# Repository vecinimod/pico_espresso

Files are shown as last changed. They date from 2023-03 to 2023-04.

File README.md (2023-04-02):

# pico espresso - $25 wifi enabled universal espresso machine PID +++ mod
A simple Raspberry Pi Pico W based espresso machine controller with support for:
+ Web interface with no addtional server (runs on mcu) using websockets for real time data
+ Shot graph generation in web ui and automatic shot timer
+ PID temperature control of boiler with duty cycled SSR
+ digital pump control profiles using PSM and robotdyn dimmer 
+ integrated shot scale with auto tareing and data recording in web app 
+ OLED display for current temperature, setpoint and SSR duty cycle
+ 1kg load cell compatible [scale case design and dimmer case](./scale/)
+ [flow meter](https://kh-technic.dk/wp-content/uploads/2020/02/AB32.pdf) measurement, logging and visualization
+ pressure transducer for real time pressure data

Can be installed on any espresso machine for temperature control but currently installed on a Calphalon temp iq

USE AT YOUR OWN RISK



picoesp





BOM ($25 to $100 depending on basic (ssr + pico + max6675) to complete (Add m6 tap, oled, load cell, dimmer, and transducer)
+ [OLED](https://www.amazon.com/gp/product/B072Q2X2LL/ref=ppx_yo_dt_b_asin_title_o00_s01?ie=UTF8&psc=1) $7
+ [SSR](https://www.amazon.com/gp/product/B08GPB7N2T/ref=ppx_yo_dt_b_asin_title_o01_s00?ie=UTF8&psc=1) $11
+ [pico w](https://www.microcenter.com/product/650108/raspberry-pi-pico-w) $6
+ [max6675](https://www.amazon.com/gp/product/B01HT871SO/ref=ppx_yo_dt_b_asin_title_o01_s00?ie=UTF8&psc=1) $7.69
+ [m6x1.0 tap and bit for thermocouple mounting on thermoblock using stock M4 hole location](https://www.amazon.com/uxcell-Spiral-Titanium-Machine-Threading/dp/B09TYS683J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) $9
+ [hx711 and 1kg load cell](https://www.amazon.com/gp/product/B08KRV8VYP/ref=ppx_yo_dt_b_asin_title_o07_s03?ie=UTF8&psc=1) $8
+ [robodyne zc triac dimmer](https://www.amazon.com/gp/product/B071X19VL1/ref=ppx_yo_dt_b_asin_title_o03_s00?ie=UTF8&psc=1) $15
+ [200 psi pressure transducer 1/8 npt](https://www.amazon.com/s?k=200+psi+pressure+transducer) $15
+ [1/8 npt female tee](https://www.amazon.com/Winmien-Fitting-Female-Diameter-Forged) $6
+ [1/8 npt to 4mm ptc connectors](https://www.amazon.com/IVLPHA-Connect-Pneumatic-Straight-Connectors/dp/B0B92BM32D) $10
+ [1k ohm and 2.2k ohm resistors](https://www.amazon.com/MCIGICM-Values-Resistor-Assortment-Resistors/dp/B06WRQS97C) $0.02 ($6 for assorment of 600)

Other parts and tools most people attempting this should already have on hand or have similar:
+ jst connectors and crimper
+ spade connectors and crimper
+ xt connectors (for wiring harness connecting mains to ssr, thermoblock)
+ 24 gauge high temp silicone coated wire
+ wire stripper
+ multimeter (handy for chasing down faulty wires and connections)
+ oscilloscope (e.g. to check flowmeter and dimmer function)
+ soldering iron
+ heat shrink tubing
+ electrical tape
+ 3d printer (for scale and cases for pico and dimmer)
+ thermal paste for thermocouple
+ donor usb cables
+ 5W usb power supply
+ [pico w shield/breadboard](https://www.amazon.com/Treedix-Compatible-Raspberry-Breakout-Flexible/dp/B091F7YSCD)

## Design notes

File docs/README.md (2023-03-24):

# Installation of software on pico w
1. Install Micropython on your pico w
2. Install the following using thonny's package manager:
    1. [picozero](https://github.com/RaspberryPiFoundation/picozero)
    2. [ssd1306](https://github.com/stlehmann/micropython-ssd1306/blob/master/ssd1306.py)
    3. [uasyncio](https://github.com/peterhinch/micropython-async/blob/master/v3/docs/TUTORIAL.md)
3. Install [microdot](https://github.com/miguelgrinberg/microdot), and it's websocket, async, and async websocket helper libraries by copying the files from github in the src folder of project that correspond to these (4 files total for microdot)
4. Add contents of lib from this project to the pico's lib directory (max6675.py, PID.py, hx711_pio.py and secrets.py)
5. Edit secrets.py accordingly for your network
6. copy main.py to your pico w
7. determine your scale factor for the loadcell and edit line 28 of main.py

# Pinout guides for each peripheral

| Max6675 | GND | VCC  | SCK | CS | SO |
| --- | --- | ---- | --- | --- | --- |
| MCU PIN Name | GND | 3.3v | GPIO21 | GPIO20 | GPIO19 |
| MCU PIN # | 23  | 36 | 27 | 25 | 24 |

| SSR | +  | \- |
| --- | -- | -- |
| MCU PIN Name | GPIO2  | GND |
| MCU PIN # | 4 | 3 |

| AB32 Flowmeter  | output | ground | 5V In |
| --- | --- | --- | ----- |
| Logic converter | HV2 | | |
| MCU PIN Name | | GND | VSYS  |
| MCU PIN # | | 38 | 39 |

| Logic converter | HV | ground | LV | LV2 |
| --- | ---- | --- | ---- | ----- |
| MCU PIN Name | VSYS | GND | 3.3v | GPIO3 |
| MCU PIN # | 39 | 38 | 36 | 5 |

| HX711 | GND | DT | SCK | VCC  |
| --- | --- | ----- | ----- | ---- |
| MCU PIN Name | GND | GPIO6 | GPIO5 | 3.3v |
| MCU PIN # | 8 | 9 | 7 | 36 |

| Robotdyn Dimmer | VCC  | GND | ZC | PSM | OUT | N | IN |
| --- | ---- | --- | --- | --- | --- | --- | ---- |
| Mains | | | | | | neutral | live |
| Pump | | | | | large gauge wire | pump thin gauge | |
| MCU PIN Name | 3.3v | GND | GPIO13 | GPIO12 | | | |
| MCU PIN # | 36 | 18  | 17 | 16 | | |

| OLED | GND | VCC  | SCL | SDA |
| --- | --- | ---- | --- | --- |
| MCU PIN Name | GND | 3.3v | GPIO15 | GPIO14 |
| MCU PIN # | 18  | 36 | 20 | 19 |

| Steam Button | Wire 1 | Wire 2 |
| --- | --- | --- |
| MCU PIN Name | GPIO9  | GND |
| MCU PIN # | 12 | 13 |

| Shot button  | Wire 1 | Wire 2 |
| --- | --- | --- |
| MCU PIN Name | GPIO10 | GND |
| MCU PIN # | 14 | 13 |

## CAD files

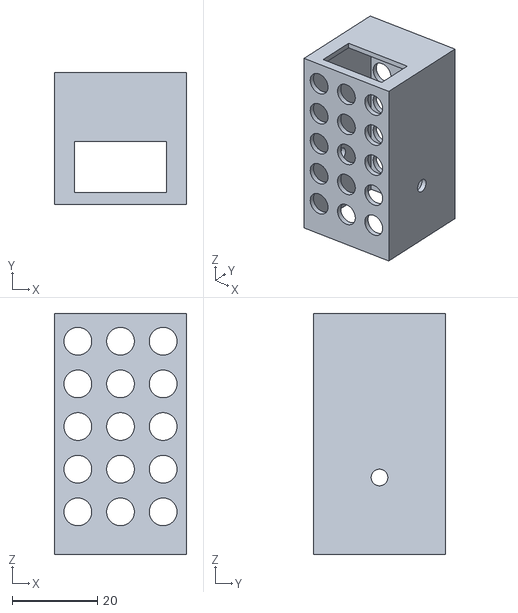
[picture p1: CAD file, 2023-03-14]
scale/dimmercase.stl
31.0 x 31.0 x 56.5

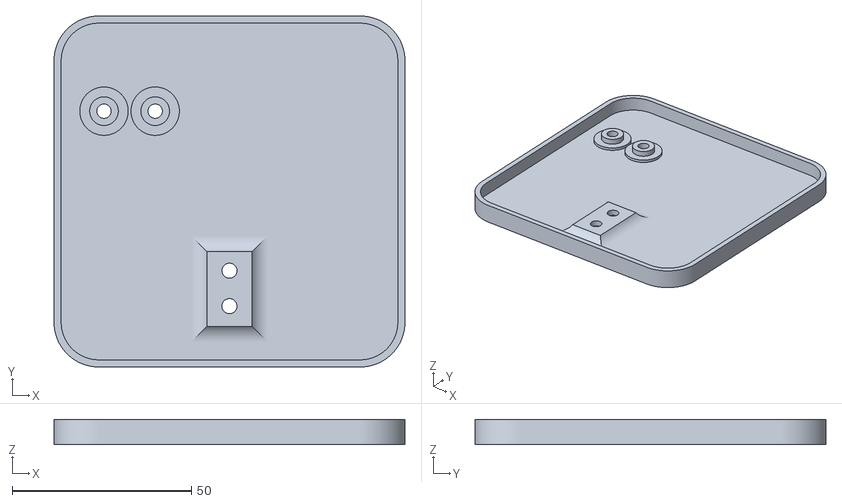
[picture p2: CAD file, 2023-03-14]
scale/bottom plate.stl
98.0 x 98.0 x 7.00

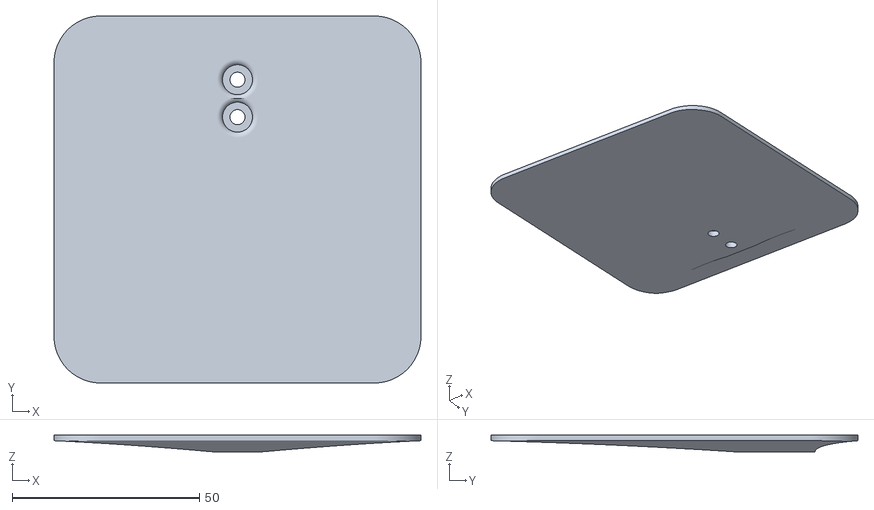
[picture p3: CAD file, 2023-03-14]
scale/topplate.stl
98.0 x 98.0 x 4.50

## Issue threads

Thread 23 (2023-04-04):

make hw config class

vecinimod, 2023-04-04:
the current setup uses default values for all pins - this could break the board or potentially peripherals for new setups
let's create an object so that we can do, e.g. the following in the pico_espresso init
```
class pinout:
    __init__(self):
        self.heater_pin = 2 #<- user configured class attributes here or read from yaml or json
        ...
class pico_espresso:
    __init__(self, pinout_instance):
    self.pinout = machine_pinout
    self.my_heater = heater(...,mypin=self.pinout.heater_pin)
    ...
```
then a new pico is
```
my_pico = pico_espresso(machine_pinout = pinout(),...)
```

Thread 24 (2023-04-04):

make watchdog for thermocouple not sensing temperature rise

vecinimod, 2023-04-04:
Protect for the condition where thermal runaway due to fault in sensing heat - may need a debug flag that turns this off when running without mains plugged in

vecinimod, 2023-04-04:
some examples of how to implement for drops in temperature and increases in temperature, but for an espresso machine this is more complicated due to stages
https://jgaurorawiki.com/thermal-runaway

vecinimod, 2023-04-04:
probably implement in steam one way (turn off steam for sure at certain timeout- add stage in profile create first line of defense) and then shots another way - preheat will also be a problem

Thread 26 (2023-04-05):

modify stage logic to have preheat be a normal stage

vecinimod, 2023-04-05:
workflow is broken for second shot after steam, as machine is still very hot, need to have preheat pump water to cool/stabilize temperature for both steam and shot

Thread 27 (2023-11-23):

max6675.py

ovimoc, 2023-11-23:
Hi,
My name is Ovidiu (ovimoc@yahoo.com),
I'm trying to take small steps with your project.
"max6675.py" seems to be missing in the "lib" directory
In the first phase, I would like to be able to monitor the temperature, weight and pressure and view the graphs on the web page.
I followed the installation steps described by you, for "uasyncio" I did not succeed with thonny's package manager but with:
"import mip
mip.install("github:peterhinch/micropython-async/v3/primitives")
mip.install("github:peterhinch/micropython-async/v3/threadsafe")"
I would like to know if it is ok?
Thank you,
I wish you a good day.

dvalentino20, 2023-11-25:
Hi for some reason I can't push a file to the repo, but here's the code for max6675.py. I am not sure about how you installed usasnycio, the only way to know if it works is to try it
```
import time
class MAX6675:
    MEASUREMENT_PERIOD_MS = 220

    def __init__(self, sck, cs, so):
        """
        Creates new object for controlling MAX6675
        :param sck: SCK (clock) pin, must be configured as Pin.OUT
        :param cs: CS (select) pin, must be configured as Pin.OUT
        :param so: SO (data) pin, must be configured as Pin.IN
        """
        # Thermocouple
        self._sck = sck
        self._sck.low()

        self._cs = cs
        self._cs.high()

        self._so = so
        self._so.low()

        self._last_measurement_start = 0
        self._last_read_temp = 0
        self._error = 0

    def _cycle_sck(self):
        self._sck.high()
        time.sleep_us(1)
        self._sck.low()
        time.sleep_us(1)

    def refresh(self):
        """
        Start a new measurement.
        """
        self._cs.low()
        time.sleep_us(10)
        self._cs.high()
        self._last_measurement_start = time.ticks_ms()

    def ready(self):
        """
        Signals if measurement is finished.
        :return: True if measurement is ready for reading.
        """
        return time.ticks_ms() - self._last_measurement_start > MAX6675.MEASUREMENT_PERIOD_MS

    def error(self):
        """
        Returns error bit of last reading. If this bit is set (=1), there's problem with the
        thermocouple - it can be damaged or loosely connected
        :return: Error bit value
        """
        return self._error

    def read(self):
        """
        Reads last measurement and starts a new one. If new measurement is not ready yet, returns last value.
        Note: The last measurement can be quite old (e.g. since last call to `read`).
        To refresh measurement, call `refresh` and wait for `ready` to become True before reading.
        :return: Measured temperature
        """
        # Check if new reading is available
        if self.ready():
            # Bring CS pin low to start protocol for reading result of
            # the conversion process. Forcing the pin down outputs
            # first (dummy) sign bit 15.
            self._cs.low()
            time.sleep_us(10)

            # Read temperature bits 14-3 from MAX6675.
            value = 0
            for i in range(12):
                # SCK should resemble clock signal and new SO value
                # is presented at falling edge
                self._cycle_sck()
                value += self._so.value() << (11 - i)

            # Read the TC Input pin to check if the input is open
            self._cycle_sck()
            self._error = self._so.value()

            # Read the last two bits to complete protocol
            for i in range(2):
                self._cycle_sck()

            # Finish protocol and start new measurement
            self._cs.high()
            self._last_measurement_start = time.ticks_ms()

            self._last_read_temp = value * 0.25

        return self._last_read_temp
```

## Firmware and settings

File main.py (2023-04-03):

import time
from json import dumps as jdump
from machine import Pin, Timer, I2C, ADC
from ssd1306 import SSD1306_I2C
from max6675 import MAX6675
from picozero import Button
from PID import PID #https://github.com/gastmaier/micropython-simple-pid/blob/master/simple_pid/PID.py
from microdot_asyncio import Microdot, Response, send_file
from microdot_asyncio_websocket import with_websocket
import uasyncio as asyncio
from random import randint
import network
from secrets import secrets
from hx711_pio import HX711

#https://stackoverflow.com/questions/74758745/how-to-run-python-microdot-web-api-module-app-run-that-is-already-an-asyncio


pin_OUT = Pin(6, Pin.IN, pull=Pin.PULL_UP)
pin_SCK = Pin(5, Pin.OUT)

hx711 = HX711(pin_SCK, pin_OUT)
#scale = 300
hx711.tare(3)
hx711.set_time_constant(.95)

def callhx2():
    value = hx711.get_value()/741.263
    return(value)
# print(callhx2())
# time.sleep_ms(3000)
# print(callhx2())

class pressure:
    def __init__(self, adcpin=1):
        self.adc=ADC(1)
    
    def read(self):
        self.volts = self.adc.read_u16() * 3.3 / 65535 #volts
        self.psi = (self.volts - .344)/(3.094-.344)*200
        self.bar = self.psi / 14.5038

    def get_bar(self):
        self.read()
        return(self.bar)

class flowmeter:
    def __init__(self, pinin=3):
        self.pin_IN = Pin(pinin, Pin.IN, pull=Pin.PULL_DOWN )
        self.last_time=0
        self.count= 0
        self.flow=0
        self.pin_IN.irq(trigger=self.pin_IN.IRQ_RISING, handler=self.update_flow)


    def update_flow(self,pin):
        self.count +=1
        
    def compute_flow(self):
        if(self.last_time==0):
            self.last_time=time.ticks_ms()
            self.last_count=self.count
            flow = 0
        else:
            this_time = time.ticks_ms()
            dt = time.ticks_diff(this_time, self.last_time)
            dct = self.count - self.last_count
            mlx1000 = .5195 * dct #1000ths of ml i.e. microliters
            flow = mlx1000 / (dt/1000)
            self.last_time = this_time
            self.last_count = self.count
        self.flow = flow

# pin_IN = Pin(3, Pin.IN, Pin.PULL_DOWN )
# def update_flow(pinn):
#     print("floooow")
# pin_IN.irq(trigger=pin_IN.IRQ_RISING, handler=update_flow)

# Replace the following with your WIFI Credentials
secrets = secrets()
SSID = secrets.SSID
SSI_PASSWORD = secrets.SSI_PASSWORD

def do_connect():
    import network
    sta_if = network.WLAN(network.STA_IF)
    if not sta_if.isconnected():
        print('connecting to network...')
        sta_if.active(True)
        sta_if.connect(SSID, SSI_PASSWORD)
        while not sta_if.isconnected():
            pass
    print('Connected! Network config:', sta_if.ifconfig())

so = Pin(19, Pin.IN)
sck = Pin(21, Pin.OUT)
cs = Pin(20, Pin.OUT)
 
max = MAX6675(sck, cs , so)
async def get_temp():
    data= max.read()
    return data
class oled_ctl:
    def __init(self, sda, scl, pwr):
        return
    def update(self, setpoint, input_, output):
        return
    
class oled_ctl_old:
    def __init__(self,sda, scl, pwr):
        i2c=I2C(1,sda=Pin(sda), scl=Pin(scl), freq=400000)
        self.oled = SSD1306_I2C(128, 64, i2c)
        self.pwr = Pin(pwr, Pin.OUT)
        self.pwr.high()
    def update(self, setpoint, input_, output):
        self.oled.fill(0)
            
        if(setpoint == 0):
            target = "SLEEPING"
        else:
            target = "Set Temp {target:.1f}"
            target = target.format(target = setpoint*1.8+32)                

        cur = "Mes Temp {cur:.1f}"
        if(input_ is None):
            cur = cur.format(cur = 0)
        else:
            cur = cur.format(cur = input_*1.8+32)
        
        duty = "Power Out {duty:.1f}%"                
        if(output is None):
            duty = duty.format(duty = 0)
        else:
            duty = duty.format(duty = output)                
            
        self.oled.text("VALENTINO Caffe", 0, 0)
        self.oled.text(target, 0, 16)
        self.oled.text(cur, 0, 32)
        self.oled.text(duty, 0, 48)
        self.oled.show()

class ssrCtrl:
    def __init__(self, WindowSize, mypid, mypin, oled):
        self.WindowSize = WindowSize
        self.pulsewidth = 20
        self.maxpulsespersec = WindowSize / self.pulsewidth #for sample period, how often can we
        self.high = False
        self.last_read = 0
        self.end_fire = 0
        self.mypid = mypid
        self.mypin = mypin
        self.oled=oled
        self.weight = 0
        

    def calc_pulse(self, temp):
        if(self.mypid.setpoint - temp > 5):
            self.output=100
        elif(temp - self.mypid.setpoint > 5):
            self.output = 0
        else:
            self.output = self.mypid(temp)
            
        print("input", temp, "setpoint", self.mypid.setpoint, "output", self.output)
        
        if(self.output is None):
            self.target_pulse = 0.1 #
        else:
            self.target_pulse = self.maxpulsespersec * self.output / 100 + 0.1 # number of pulses to fire on out of possible in sample period
        if(self.target_pulse > self.maxpulsespersec):
            self.target_pulse = self.maxpulsespersec
        self.fire_every_pulses = self.maxpulsespersec / self.target_pulse
        self.fire_every_ms = self.pulsewidth * self.fire_every_pulses
            
    async def pulse(self):
        now = time.ticks_ms()

        if(self.last_read==0 or now - self.last_read > self.WindowSize):        #new measurement and target pulse
            self.mypin.low()
            self.last_read = now
            temp=await get_temp()
            self.calc_pulse(temp)    
            self.oled.update(self.mypid.setpoint, await get_temp(), self.output)
            
        if(self.target_pulse >= 1 and self.output < 100): #calling for output

            if(now > self.end_fire ):
                #end pulse          
                self.mypin.low()
                self.high = False
            
            if self.end_fire==0 or (now > self.next_fire and not self.high):
                #new pulse now set it up
                self.start_fire = time.ticks_ms()
                self.end_fire = self.start_fire + self.pulsewidth
                self.next_fire = self.end_fire + self.fire_every_ms
                self.mypin.high()
                self.high = True
                
        elif(self.output==100):
            self.mypin.high()
    
    def reset(self):
        if(self.target_pulse>0):
            self.target_pulse = 0
            self.output = 0
            self.last_read = 0 

#define app
#https://www.donskytech.com/using-websocket-in-micropython-a-practical-example/
#https://stackoverflow.com/questions/74758745/how-to-run-python-microdot-web-api-module-app-run-that-is-already-an-asyncio
app = Microdot()
Response.default_content_type = 'text/html'

@app.route('/')
async def index(request):
    asyncio.sleep_ms(1)
    print("index request")
    return send_file('index.html')

@app.route('/echo')
@with_websocket
async def echo(request, ws):
    while True:
        asyncio.sleep_ms(1)
        data = await ws.receive()
        print(data)
        target = "Set Temp {target:.1f}"
        my_espresso.set_shot_temp(int(data))
        target = target.format(target = my_espresso.user_shot_temp)
        asyncio.sleep_ms(1)
        await ws.send(target)
        
@app.route('/mode')
@with_websocket
async def echo(request, ws):
    while True:
        asyncio.sleep_ms(100)
        data = await ws.receive()
        print(data)
        asyncio.sleep_ms(1)
        hx711.tare(3)
        if(my_espresso.mode == "shot"): #check machine mode has to be in shot mode
            my_espresso.ui_mode_change_request()
        else:
            print("Error gui asked for shot mode when not physically in shot mode, turn dial")
        
@app.route('/data')
@with_websocket
async def data(request, ws):    
    while True:
        await asyncio.sleep_ms(my_espresso.sample_period)
        temp = await get_temp()
 
        weight = callhx2()
        myflow.compute_flow()
        data_str = jdump({"time":my_espresso.mode_elapsed_time/1000,"temperature":temp,
                          "output":my_espresso.myssr.output, "setpoint":my_espresso.mypid.setpoint,
                          "weight":weight, "mode":my_espresso.mode,"mode_change":my_espresso.flag_ui_mode_change,
                          "pump_output":my_espresso.mypump.output,
                          "flow":myflow.flow, "pressure":mypressure.get_bar()})
        my_espresso.flag_ui_mode_change = False
        await ws.send(data_str)

        
class pump:
    def __init__(self, profile, psm):
        self.profile = profile
        self.stage = 0
        self.time_start_stage=0
        self.psm = psm
        self.output=0
        self.set_profile(profile)
    
    def set_profile(self, profile):
        self.profile = profile
        cumultime = 0

        for k in sorted(self.profile.keys()):
            self.profile[k]["start"] = cumultime 
            self.profile[k]["end"] = cumultime + self.profile[k]["duration"]
            cumultime = self.profile[k]["end"]

        print("updated pump profile:", self.profile)
    
    def update_shot_pump_output(self, time_ms, mass):
        _output = -1
        time_s = time_ms / 1000
        if(self.stage == 0):
            self.time_start_stage = time_s
            self.stage=1
            
        if(mass<0):
            mass = 0
            
        if(self.stage<=len(self.profile)):            
            if(time_s - self.time_start_stage > self.profile[self.stage]["duration"] or self.profile[self.stage]["max_mass"] < mass):
                self.stage += 1
                self.time_start_stage = time_s
            if(self.stage<=len(self.profile)):         
                self.output = ((time_s - self.time_start_stage) / self.profile[self.stage]["duration"]) * (self.profile[self.stage]["pump_end"] - self.profile[self.stage]["pump_start"]) + self.profile[self.stage]["pump_start"]
        else:
            self.output = 0

    def run_pump(self, start_time, current_time, mass_update_intvl=250):
        timenow = time.ticks_diff(current_time, start_time)
        if(timenow<100):
            self.mass=0
        if(timenow%mass_update_intvl<=10):
            self.mass = callhx2()
        self.update_shot_pump_output(timenow, self.mass)
        self.psm.set_output(self.output)
#         if(self.stage<=len(self.profile) and timenow%1000==0):
#         if(timenow%1000==0):
#             myflow.compute_flow()
#             if(self.stage<=len(self.profile)):
#                 print("time", timenow/1000,"stage",self.profile[self.stage]["name"],
#                       "output", self.output, "mass", self.mass, "flowct", myflow.count,
#                       "flow", myflow.flow)
#         else:
#             return
    def reset(self):
        self.psm.set_output(0)
        self.stage=0
        
    def test_output(self):
        startt=time.ticks_ms()
        timeno = 0
        mass=0
        
        while(True):
            timeno = time.ticks_diff(time.ticks_ms(),startt)
            self.update_shot_pump_output(timeno, mass)
            self.psm.set_output(self.output)
            if(timeno % 1000 == 0):
                mass = callhx2()
                if(self.stage<=len(self.profile)):
                    print("time", timeno/1000,"stage",self.profile[self.stage]["name"], "output", "shoto", self.output, "selfo", self.output, "mass", mass)
                else:
                    return

class psm:
    def __init__(self, psm_pin=12, zc_pin=13):
        self.psm_pin = Pin(psm_pin, Pin.OUT)
        self.zc_pin = Pin(13, Pin.IN, pull=Pin.PULL_DOWN)
        self.zc_pin.irq(trigger=self.zc_pin.IRQ_RISING, handler=self.pulse)
        self.high=False
        self.output=0
        self.start_time= time.ticks_ms()
        self.last_fire = self.start_time
        self.count=0
        self.mypid = PID(40, 0.05, 0.05, setpoint=10, scale='ms',
                         output_limits=[0, 100], proportional_on_measurement=False)

    def set_output(self, req_output):
        if(req_output > 100):
            req_output = 100
        elif(req_output < 0):
            req_output = 0
            
        self.output = req_output

    def pulse(self, pin):
        if(self.output==100):
            self.psm_pin.high()
        else:
            if(self.count*100 % (10000//(100-self.output)) < 100): # ct * 100 % (100//((100-output)*100))
                self.psm_pin.low()
            else:
                self.psm_pin.high()
                
        if(self.count==100):
            self.count=1
        else:
            self.count+=1
        
    def sim(self):
        oo = 0
        startt=time.ticks_ms()
        timeno = 0
        input=0
        while(True):
            timeno = time.ticks_diff(time.ticks_ms(),startt)
            input = timeno/100000 *.2 * oo - randint(0,100)/50
            if(input<0):
                input = 0
            if(input>10):
                input=10
            if(timeno % 1000 == 0):
                oo = self.mypid(input)
                print("time", timeno, "input",input, "output", oo, "seto", self.output)
                self.set_output(oo)
            
        
# a class to manage the loop, run both control + sensor and app tasks
class espresso:
    def __init__(self, oled, shot_profile, steam_profile, sample_period=1000, ssr_pin=2, steam_btn_pin=9, shot_btn_pin=10):

        self.default_shot_temp = 101
        self.user_shot_temp = 0
        self.default_steam_temp = 150
        self.user_steam_temp = 0

        self.sample_period = sample_period
        
        self.steamButton = Button(steam_btn_pin)
        self.shotButton = Button(shot_btn_pin)
        
        self.mypin = machine.Pin(ssr_pin, Pin.OUT)
        self.oled = oled
        
        self.shot_profile = shot_profile
        self.steam_profile = steam_profile
        
        self.last_mode = None
        self.mode = None
        self.mode_change = False
        self.flag_ui_mode_change = False
        self.ui_mode_change_requested = False
        
        self.loop = asyncio.get_event_loop()
        self.start_time = time.ticks_ms()
        
    def call__async_main(self):
        task1 = self.loop.create_task(self.run_machine(self.loop))
        task2 = self.loop.create_task(self.start_web_server())
        self.loop.run_forever()

    def set_shot_temp(self, temp):
        self.user_shot_temp = temp
        
    async def start_web_server(self):
        do_connect()
        await app.start_server(port=5000, debug=True)
        
    def ui_mode_change_request(self):
        self.ui_mode_change_requested = True
        
    def sense_mode(self):
        if(self.shotButton.is_pressed and self.steamButton.is_pressed):
            mode = "steam"
        elif(self.shotButton.is_pressed or self.steamButton.is_pressed):
            mode = "shot"
        elif(not self.shotButton.is_pressed and not self.steamButton.is_pressed):
            mode = "sleep"
        else:
            mode = "sleep"
        
        if(self.last_mode is not None and mode != self.last_mode) or self.ui_mode_change_requested:
            self.mode_change=True
            if(self.last_mode!="shot"):#enable that we can save the graph from getting reset at 0
                self.mode_start_time = time.ticks_ms()
        else:
            self.mode_change = False
            
        self.last_mode = mode
        self.mode = mode

    def run_mode(self):
        if(self.mode_change):
            self.flag_ui_mode_change = True
            self.ui_mode_change_requested = False
            self.mypump.reset()
            if(self.mode=="steam"):
                self.mypid.reset()
                if(self.user_steam_temp>0):
                    self.mypid.setpoint = self.user_steam_temp
                else:
                    self.mypid.setpoint = self.default_steam_temp
                self.mypump.set_profile(self.steam_profile)
                
            elif(self.mode=="shot"):
                self.mypid.reset()
                if(self.user_shot_temp>0):
                    self.mypid.setpoint = self.user_shot_temp
                else:
                    self.mypid.setpoint = self.default_shot_temp
                self.mypump.set_profile(self.shot_profile)
                
            elif(self.mode=="sleep"):
                self.mypin.low()
                self.mypid.setpoint = 0
                self.mypid.reset()
                self.mypid.automode = False
                self.myssr.reset()
                
        self.mode_elapsed_time = time.ticks_diff(time.ticks_ms(),self.mode_start_time)


    async def run_machine(self, parent_loop):        
        self.mypid = PID(1.7, 0.05, 0.05, setpoint=0, scale='ms')
        self.mypid.output_limits = (0, 100)
        
        self.myssr = ssrCtrl(self.sample_period, self.mypid, self.mypin, self.oled)
        
        self.mypsm = psm(12,13)
        self.mypump = pump(self.shot_profile, self.mypsm)
        self.mode_start_time = time.ticks_ms()

        while(True):
            self.current_time = time.ticks_ms()
            self.elapsed_time = time.ticks_diff(self.start_time, self.current_time)
            self.sense_mode()
            self.run_mode()
            
            if(self.mode=="shot"):
                self.mypump.run_pump(self.mode_start_time, time.ticks_ms(), 1000)
                
            elif(self.mode=="steam"):
                self.mypump.run_pump(self.mode_start_time, time.ticks_ms(), 1000)
                
            if(time.ticks_ms() > shutdownTime):
                await self.mypin.low()
                parent_loop.stop()
                break
            
            elif(self.mypid._last_input is not None and self.mypid._last_input > 155): #exit if 104c or 220f reached
                await  self.mypin.low()
                parent_loop.stop()
                break
            
            #mypsm.pulse()
            await self.myssr.pulse()
            await asyncio.sleep_ms(1)

#show that we're on
led = machine.Pin("LED", machine.Pin.OUT)
led.high()

sample_period=1000 # how often to run PID output calculation
windowStartTime = time.ticks_ms()
shutdownTime = windowStartTime + 20 * 60 * 1000 # turn off after 10 minutes

#setup oled
myoled = oled_ctl(14, 15, 16)

#setup pump

shot_profile = {
    1: {"name":"pre-infusion","duration":7, "pump_start":100, "pump_end":100, "max_mass":3},
    2: {"name":"wait","duration":25, "pump_start":0, "pump_end":0, "max_mass":100},
    3: {"name":"ramp","duration":4, "pump_start":35, "pump_end":75, "max_mass":100},
    4: {"name":"pour","duration":60, "pump_start":25, "pump_end":10, "max_mass":45}
            }

steam_profile = {
    1: {"name":"preheat","duration":20, "pump_start":0, "pump_end":0, "max_mass":100},
    2: {"name":"steam","duration":250, "pump_start":2, "pump_end":2, "max_mass":100}
            }
myflow=flowmeter()
mypressure = pressure()

my_espresso = espresso(myoled, shot_profile, steam_profile) #TODO add pump to espresso as argument
my_espresso.call__async_main()

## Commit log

2023-03-11 replace PID and clean ssr
    [main.py]
2023-03-11 fix ws and async passes
    [main.py]
2023-03-12 Major improvements (#3)
    * updates secrets approach and clean up
    * Create secrets.py
    * add shot pull button and state mgmt
    * Update index2.html
    * Update index2.html
    * Update main.py
2023-03-12 add timer (#4)
    * add timer
    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
2023-03-14 Scale (#13)
    * Create tmp.txt
    * Add files via upload
    * Delete tmp.txt
    * Update README.md
    [bottom plate.stl, dimmercase.stl, topplate.stl]
2023-03-19 Add pump control (#17)
    * Update readme
    * stop dropping shot graph
    * stop dropping shot graph in ui
    * Add pump profiling control based on time and weight
    * add pump integration
    * Create wiring.md
    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
2023-04-02 Update pump psm (#21)
    * improve psm and add steam
    * add gif, parts, and tools
    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
